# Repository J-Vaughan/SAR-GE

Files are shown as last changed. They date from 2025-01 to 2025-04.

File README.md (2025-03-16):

# SAR-GE

SAR-GE is a plan for a satellite using an SAR (Synthetic Aperture Radar) to
surveil Greenhouse Emissions over the entire domain of Canada. This project is
for Spacecraft Design I (AERO 3841) at Carleton University, and the defined
project variables are listed in the [Requirements](#Requirements) section.

> IMPORTANT: If you are currently taking AERO 3841, you are *not* permitted to
> use any part of this project to help you, for risk of academic misconduct.

This repository is meant to showcase my analysis and writing skills. ~~And, just
for fun, I'm going to try to do all of this with free, open-source software.~~
Why not use the tools given to me? I'll be using Ansys STK 12 and SolidWorks
2024.

## Mission Statement

From the project guidelines written by Professor T. Kaya, the main goal of this
mission is to monitor gas and oil pipelines from space. The payload is a SAR
consuming an average power of 350 W with a mass of 200 kg, housed in a
1 m by 0.5 m by 0.5 m (presumably) rectangular housing. The required resolution
is 5 m, and the ground swath width is 100 km. The coverage area per image is
100 x 100 km^2, and the whole country (Canada) needs to be imaged within
14 days. The master Earth station is the Gatineau Satellite Ground Station, with
Prince Albert station as a backup. The useful lifetime is 5 years, and the time
to deployment is 3 years.

# Requirements

The requirements listed in this section have been prescribed by the project
document.

## Communications
### Payload Data
- Required resolution of 5 m
- Area covered per image of 100 km x 100 km
- Ground swath width of 100 km
- Entire country must be imaged within 14 days

### Housekeeping Data
- The communications package must include the following data in addition to the
  payload data:
  | Data | Bits |
  | ---- | ---- |
  | Error Detection | 3 b per image size in bytes |
  | Latitude | 32 b per image |
  | Longitude | 32 b per image |
  | Altitude | 32 b per image |
  | Time | 64 b per image |
  | Synchronization | 24 b per image |
- Housekeeping data is sampled 100 times per minute with 16 bits
  per sample.

## Power
- Payload average power of 350 W.

## ADCS
- 1 degree accuracy for each of the three axes, and 0.1 degree accuracy for
  attitude determination.

## GNS
- Orbit should be maintained within 5 km of accuracy.

## Thermal
- Upper temperature limit of 50 degrees celsius, lower limit of -5 degrees, with
  a 5 degree margin on both values.
- Payload to be maintained at 20 degrees celsius with variation of less than
  1 degree on either side.

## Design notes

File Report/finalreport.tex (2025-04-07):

\documentclass[9pt]{article}
\usepackage[letterpaper, margin=2cm]{geometry}
\usepackage[utf8]{inputenc}
\usepackage[sfdefault]{inter}
\usepackage[T1]{fontenc}
\usepackage{amsmath}
\usepackage{graphicx, caption}
\usepackage{xcolor}
\usepackage{subcaption}
\usepackage{siunitx}
\usepackage{subfig}
\usepackage{booktabs}
\usepackage{tabularx}
\usepackage{multirow}
\usepackage{pdflscape}
\usepackage{mhchem}
\let\temp\rmdefault
\usepackage{fourier}
\let\rmdefault\temp

\usepackage[
  backend=biber,
  style=ieee
]{biblatex}
\addbibresource{spacecraft.bib}

% Title Page
\title{\Huge SARGE\\\Large Final Report}
\author{Jimmy Vaughan\\(101 156 687)}

\begin{document}
\begin{figure}[t]
  \centering
  
\end{figure}
\maketitle
\pagenumbering{gobble}
\clearpage
\tableofcontents
\clearpage
\pagenumbering{arabic}
\section{Introduction}
SARGE, \textbf{S}ynthetic~\textbf{A}perture~\textbf{R}adar:~\textbf{G}reenhouse~\textbf{E}missions, is a satellite platform designed to monitor for potential leaks of cross-Canada pipelines using synthetic aperture radar.
This report details a prelimnary design that should provide a solid starting point for further analysis and refinement.
Assumptions and estimations are necessary at this stage of development, and their presence is clearly noted in the following sections on analysis.

Preliminary design drawings are avaiable in the last appendix, Appendix~\ref{app:julia}.

\subsection{Primary Mission Objectives}
  The primary mission objective of SARGE is to monitor the entirety of Canada for the presence of greenhouse gasses that would indicate leaks in the transcontinental petrochemical pipelines.
  To this end, SARGE covers all of contiguous Canada, but does not directly cover the many islands in the far north of the territories.
  This should be acceptable, since there are no pipelines in those areas, and there is really only one pipeline above Hudson's Bay, ending just north of Mackenzie Bay, past Inuvik,~N.W.T.~\cite{pipelines}.
\subsection{Secondary Mission Objectives}
  Since SARGE covers the entirety of Canada (and Alaska, U.S.) any application of regular monitoring could be co-located on the satellite.
  Wildfire monitoring/detection, all industrial greenhouse gas emissions, and even meteorology.
  One of the only terrestrial applications SARGE is unsuited for is communications, as it is out of sight for about 2/3 of each day.

\section{Orbit Selection}
The assigned mission requirements state that this satellite is to image the entirety of Canada at least once every 14~days.
To satisfy this requirement, a geosynchronous orbit with a nonstandard high inclination (\ang{121}) was chosen.
The ground track of a conical SAR (shown in Figure~\ref{fig:groundtrack}) with a minimum elevation angle of \ang{75} covers the entirety of contiguous Canada.

\begin{figure}[hb]
  \centering
  \captionsetup{width=.75\linewidth,font={small},labelfont={bf}}
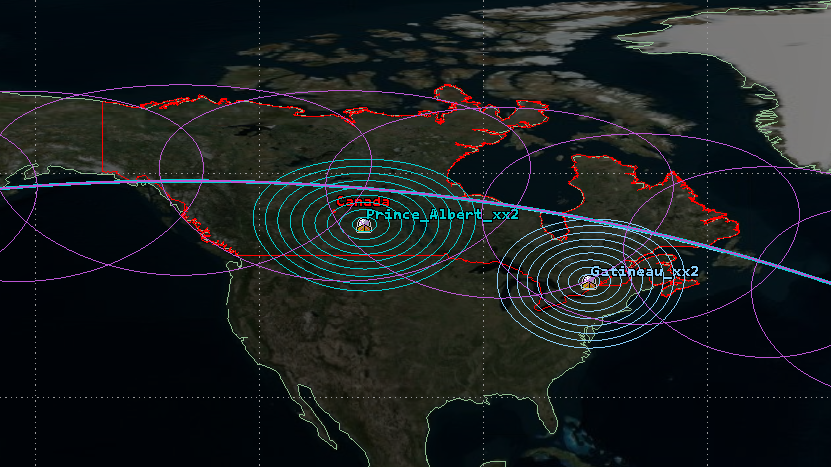
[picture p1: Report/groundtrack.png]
  
  \caption{Ground swath of SARGE over continental Canada. Ground stations are shown in teal and sky blue, and the majority of Canada is outlined in red ($A\approx\qty{8.342e6}{\square\kilo\metre}$). The magenta circles show the coverage of the SAR beam at some discrete points in time.}
  \label{fig:groundtrack}
\end{figure}

The orbital parameters are summarized in Table~\ref{tab:orbit}.
We can see that the chosen orbit is a circular retrograde orbit with a period of about one sidereal day.
This regularity allows the satellite to image, process, and transmit one~fourteenth of Canada each day, with a consistent and regular ground station access window.

\begin{table}[h]
  \centering
  \captionsetup{width=.75\linewidth,font={small},labelfont={bf}}
    \begin{tabular}{r S|r S}
      \toprule
      \multicolumn{4}{c}{Basic Orbital Parameters}\\
      \midrule
      Period $P$ & \qty{86170.5}{\second} & Arg. of Perigee $\omega$ & \ang{0} \\
      Eccentricity $\epsilon$ & \num{0.0} & LAN $\Omega$ & \ang{50} \\
      Inclinination $i$ & \ang{121} & True Anomaly $\nu$ & \ang{30} \\
      \midrule %\midrule
      \multicolumn{4}{c}{Derived Quantities}\\
      \midrule
      Orbit Radius $r$ & \qty{42166.26}{\kilo\metre} & Orbital Altitude $h$ & \qty{35788.12}{\kilo\metre} \\
      Velocity $v$ & \qty{3.074}{\kilo\metre\per\second} & Orbits per Day $n$ & \qty{1.002663}{\per\day} \\
      \bottomrule
    \end{tabular}
    \caption{Orbital parameters and convenient derived quantities.}
    \label{tab:orbit}
\end{table}

At high altitudes, like GEO, the gravitational forces of the Sun and the Moon become significant, but air drag is generally negligible~\cite[p. 81]{sse}.
As well, the high inclination of SARGE allows it to avoid most of the clutter in the GEO belt, since most of the objects are within <\ang{5} inclination~\cite[p. 140]{sme}.
Another advantage is the lack of an eclipse time in service (there may be a short eclipse during transit to orbit), as shown in Figure~\ref{fig:eclipse} in Section~\ref{sys:power}.
Stationkeeping requirements are also quite low, as explored in Appendix~\ref{app:stnkeep} and mentioned in Section~\ref{sys:prop}, since the oblateness of Earth is primarily a factor in lower inclination orbits.

\section{Spacecraft Bus}
\subsection{Mass and Power Budget}
According to David Everett of the NASA Goddard Space Flight Center, the first of the three steps of mass estimation is ``A rough order of magnitude based on payload mass''~\cite[p. 399]{sme}.
Given that sentiment, and approximate sizing of the power array (see Section~\ref{sys:power}), the initial mass estimate is based on data representative of mission type \textit{and} historical data given in Table~14-18, which can be found in Appendix~\ref{app:refs}, Figure~\ref{fig:1418}, and summarized in Table~\ref{tab:mass}, with comments noted in the third column.

\begin{table}[h]
  \centering
  \captionsetup{width=.75\linewidth,font={small},labelfont={bf}}
  %\begin{tabularx}{.8\linewidth}{l|r r X}
  \begin{tabular}{l|r r l}
    \toprule
    Subsystem & Mass\% & Mass & Comments \\
    \midrule
    Payload & \qty{32}{\percent} & \qty{200}{\kilo\gram} & Provided in requirements \\
    Structure \& Mechanisms & \qty{24}{\percent} & \qty{150}{\kilo\gram} & Taken from Table~14-18\\
    Thermal Control & \qty{6}{\percent} & \qty{36.}{\kilo\gram} & \qty{11}{\kilo\gram} taken from Power subsystem\\ 
    Power (incl. harness) & \qty{13}{\percent} & \qty{82}{\kilo\gram}&Less than usual since no eclipse\\
    TT\&C & \qty{4}{\percent} & \qty{25}{\kilo\gram}&Taken from Table~14-18\\
    Data Processing & \qty{3}{\percent} & \qty{19}{\kilo\gram}&''\\
    ADCS & \qty{8}{\percent} & \qty{50}{\kilo\gram}& \qty{13}{\kilo\gram} taken from Power\\
    Propulsion & \qty{7}{\percent} & \qty{44}{\kilo\gram}&Taken from Table~14-18\\
    Other & \qty{3}{\percent} & \qty{19}{\kilo\gram}&''\\
    \midrule 
    Total Dry Mass & \qty{100}{\percent} & \qty{625}{\kilo\gram} & \\
    Propellant & \qty{142}{\percent} & \qty{885}{\kilo\gram} & Double expected amount in Table~14-18\\
    Kick motor & \qty{12}{\percent} & \qty{75}{\kilo\gram} & Estimated mass of a jettisonable liquid motor\\
    \midrule 
    Wet Mass & & \qty{1585}{\kilo\gram} & \\
    \bottomrule
  \end{tabular}
  \caption{Preliminary mass budget estimation, based on provided payload mass and the listing for ``High Earth'' in the SME-SMAD~\cite{sme}.}
  \label{tab:mass}
\end{table}

The breakdown of the power subsystem is available in Table~\ref{tab:powerbreakdown} in Section~\ref{sys:power}.
Historical basis for the amount of propellant needed was insufficient for this particular satellite, primarily because of the steep inclination and the high-$\Delta V$ maneuvers required, detailed in Section~\ref{sys:prop}.
The total wet mass still comes in at far less than the SpaceX Falcon~9's maximum lift-off mass of \qty{5800}{\kilo\gram} (Table~\ref{tab:launchertrade}), so a shared launch is still feasible (especially given the compact nature of SARGE).

  Like the Mass Budget in Table~\ref{tab:mass}, the preliminary power budget below in Table~\ref{tab:power} is based on David~Everett's chapter of the SME-SMAD, Table~14-20 (Appendix~\ref{app:refs}, Figure~\ref{fig:1420}).
  This time, however, a modification to the suggested weights in Table~14-20 was made to accomodate the two one-axis solar array gimbals notes in Section~\ref{sec:configuration}. 
The payload power proportion was thus lessened by \qty{2}{\percent}, from \qty{35}{\percent} to \qty{33}{\percent} to give a corresponding power proportion of \qty{2}{\percent} to the Structures~\&~Mechanisms subsystem.
The solar array and battery sizing calculations are presented in Section~\ref{sys:power}.

\begin{table}[h]
  \centering
  \captionsetup{width=.75\linewidth,font={small},labelfont={bf}}
  \begin{tabular}{l|r r l}
    \toprule
    Subsystem & Power\% & Avg. Power & Comments \\
    \midrule
    Payload & \qty{33}{\percent} & \qty{350}{\watt} & Specified in requirements, mod. from Table~14-20 \\ 
    Structure \& Mechanisms & \qty{2}{\percent} & \qty{21}{\watt} & Mod. from Table~14-20 \\
    Thermal & \qty{14}{\percent} & \qty{148}{\watt} & Taken from Table~14-20 \\
    Power (incl. harness) & \qty{7}{\percent} & \qty{75}{\watt} & ''\\
    TT\&C & \qty{16}{\percent} & \qty{170}{\watt} & ''\\
    Data Processing & \qty{10}{\percent} & \qty{106}{\watt} &''\\
    ADCS & \qty{16}{\percent} & \qty{170}{\watt}&''\\
    Propulstion & \qty{2}{\percent} & \qty{21}{\watt} & ''\\
    \midrule
    Total & \qty{100}{\percent} & \qty{1061}{\watt} &\\
    \bottomrule
  \end{tabular}
  \caption{Preliminary power budget estimation, based on provided payload mass and the listing for ``High Earth'' in the SME-SMAD~\cite{sme}, modified to allow for powered mechanisms.}
  \label{tab:power}
\end{table}

\subsection{Configuration}\label{sec:configuration}
The configuration of SARGE is a nadir-pointing 3-axis stabilized solar-powered satellite.
The two solar arrays are gimbaled in one axis with a range of $\pm\ang{10}$ to account for the slight variation in the spacecraft's orientation with respect to the sun as it travels along its orbital path (this angle was found in Appendix~\ref{app:orbplanes}).
The size of the spacecraft can be estimated using the relations listed in Slideshow~3, Configuration, and shown in Table~\ref{tab:sizeest} below.

\begin{table}[h]
  \centering
  \captionsetup{width=.75\linewidth,font=small,labelfont=bf}
  \begin{tabular}{lll}
    \toprule
    Characteristic & Equation & Estimate \\
    \midrule
    Volume (\si{\meter\cubed}) & $V=0.01M$ & \qty{15.85}{\meter\cubed}\\
    Linear Dimension (\si{\meter}) & $L=0.25M^{1/3}$ & \qty{2.91}{\meter}\\
    Body Area (\si{\meter\squared}) & $A_b=V/L$ & \qty{5.44}{\meter\squared}\\
    Moment of Inertia (\si{\kilo\gram\meter\squared}) & $I=0.01M^{5/3}$ & \qty{2155}{\kilo\gram\meter\squared}\\
    \bottomrule
  \end{tabular}
  \caption{Estimate of spacecraft dimensions, where $M$ is spacecraft wet mass in \si{\kilo\gram}.}\label{tab:sizeest}
\end{table}

(Comment on the estimations). The mark is actually for assumptions for calculations? Idk, I modelled the satellite to fit the payload bruh.

An annotated isometric view of the preliminary design/layout is shown in Figure~\ref{fig:iso}.

\begin{figure}[h]
  \centering
  \captionsetup{width=.75\linewidth,font=small,labelfont=bf}
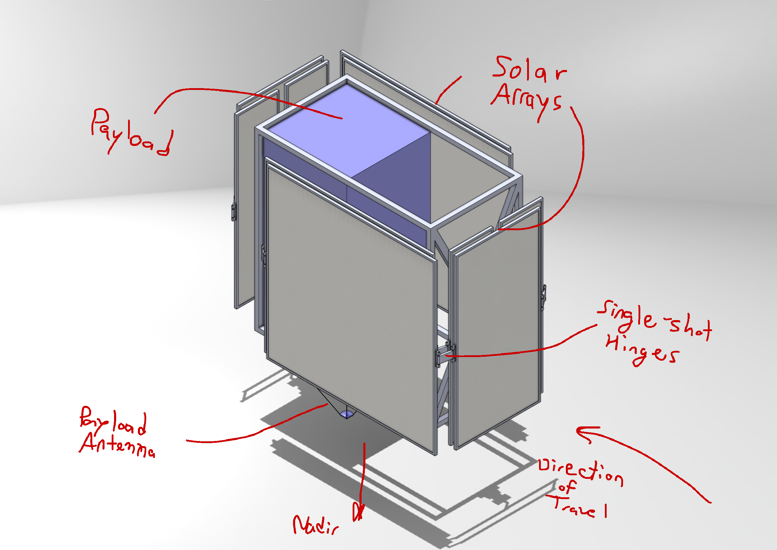
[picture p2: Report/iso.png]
  
  \caption{Isometric view of the satellite with annotation in red to aid understanding.}
  \label{fig:iso}
\end{figure}

As can hopefully be seen, the major components currently include 2 solar arrays, articulated only for launching, via single-shot hinges at each meeting point.
These arrays are gimbaled in one axis, shown in the front view, Figure~\ref{fig:front}.
The direction of travel is shown in Figure~\ref{fig:iso}, as well as the nadir pointing direction.

\begin{figure}[h]
  \centering
  \captionsetup{width=.75\linewidth,font=small,labelfont=bf}
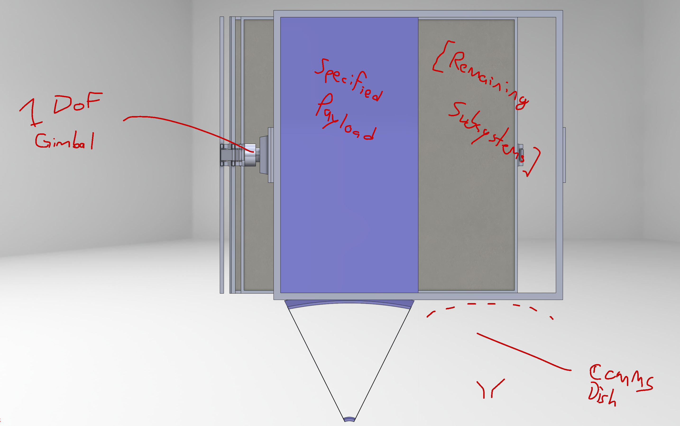
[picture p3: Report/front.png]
  
  \caption{Front view of SARGE with annotation in red. One of the solar panel arrays is hidden so as not to obstruct the interior of the frame.}
  \label{fig:front}
\end{figure}

Since the masses of the solar arrays are identical, and they are symmetric about the nadir axis, and since the mass proportion of the payload is only around \qty{32}{\percent} of the total dry mass, the remaining subsystems should make it so that the center of mass is not located within the payload container.
This means that an ADCS system with reaction wheels should be able to be located directly in line with all three axes relative to the center of inertia, so pointing should be easily controllable.
The remaining subsystems will all ideally fit in the remaining payload-sized area to the right of the payload in Figure~\ref{fig:front}.

More engineering drawings are available in Appendix~\ref{app:julia}.

Drawings (3.5)

Justification (2)

\subsection{Preliminary Design of Spacecraft Subsystems}
\subsubsection{Communications Subsystem}\label{sys:comms}
Based on both slide deck 6, ``TTC'', and select portions of the SME-SMAD, the uplink and downlink link budgets are summarized in Table~\ref{tab:link}.
As well, the downlink and uplink frequencies were chosen according to Professor~Jim~Wight's course handout for ELEC~4509.
It's noted in that handout that frequency ranges 7.25-7.30~GHz and 7.975-8.025~GHz are reserved for downlink and uplink satellite communications, respectively~\cite[II, p. 3]{commlinks}.
The downlink budget was conceived using the data rate/budget calculations in Appendix~\ref{app:linkbudget}.
As a quick summary, the amount of data transmitted per 14 days is about \qty{1}{\tera\byte}, with a daily access window of \qty{9.5}{\hour} and a downlink data rate during that window of about \qty{2.5}{\mega\byte\per\second}, for a (QPSK-encoded) bandwidth of about \qty{12}{\mega\hertz} on a \qty{7.275}{\giga\hertz} carrier.
\begin{table}[h]
  \centering
  \captionsetup{width=.75\linewidth,font=small,labelfont=bf}
  \begin{tabular}{c|rl|l}
    \toprule
    Uplink & Value & Unit & Comments \\
    \midrule
    $P_t$ & \num{23.01} & \si{\decibel\watt} & \qty{200}{\watt} ground transmitter assumed\\
    $G_t$ & \num{57.74} & \si{\decibel} & Eq.~\ref{eq:200}\\
    $L_\text{path}$ & \num{202.68} & \si{\decibel} & Eq.~\ref{eq:203}\\
    $L_\text{point}$ & \num{18.42} & \si{\decibel} & Eq.~\ref{eq:303}\\
    $L_\text{atmosphere}$ & \num{10.00} & \si{\decibel} & Assumed\\
    $k$ & \num{-228.60} & \si{\decibel\joule\per\kelvin} & \\
    $B$ & \num{37.00} & \si{\decibel\hertz} & Eq.~\ref{eq:201}\\
    $G_r$ & \num{6.49} & \si{\decibel} & Figure~\ref{fig:hfss}\\
    $T$ & \num{14.31} & \si{\decibel\kelvin} & Assumed\\
    \midrule
    ${C/N}_\text{achieved}$ & \num{33.42} & \si{\decibel} & Eq.~\ref{eq:uplinkachieved}\\
    ${C/N}_\text{required}$ & \num{8.16} & \si{\decibel} & Eq.~\ref{eq:202}\\
    \midrule
    Margin & \num{25.27} & \si{\decibel}& \\
    \bottomrule \toprule
    Downlink & Value & Unit & Comments\\
    \midrule
    $P_t$ & \num{20.00} & \si{\decibel\watt} & \qty{100}{\watt} of \qty{170}{\watt} estimated in power budget\\
    $G_t$ & \num{28.61} & \si{\decibel} & Eq.~\ref{eq:100}\\
    $L_\text{path}$ & \num{201.85} & \si{\decibel} & Eq.~\ref{eq:101}\\
    $L_\text{point}$ & \num{0.36} & \si{\decibel} & Eq.~\ref{eq:302}\\
    $L_\text{atmosphere}$ & \num{10.00} & \si{\decibel} & Assumed\\
    $k$ & \num{-228.60} & \si{\decibel\joule\per\kelvin} & \\
    $B$ & \num{70.77} & \si{\decibel\hertz} & Eq.~\ref{eq:downlinkbw}\\
    $G/T$ & \num{46.94} & \si{\decibel\per\kelvin} & Eq.~\ref{eq:minGT}\\
    \midrule
    ${C/N}_\text{achieved}$ & \num{41.17} & \si{\decibel} & Eq.~\ref{eq:downlinkachieved}\\
    ${C/N}_\text{required}$ & \num{11.52} & \si{\decibel} & Eq.~\ref{eq:102}\\
    \midrule
    Margin & \num{29.65} & \si{\decibel} & \\
    \bottomrule
  \end{tabular}
  \caption{Preliminary link budget, based on noted assumptions and analyses detailed in Appendix~\ref{app:linkbudget}.}
  \label{tab:link}
\end{table}

Unlike the preliminary design, for this design the uplink receiving antenna (i.e. the one on the spacecraft) is no longer the same as the parabolic downlink antenna.
The concern is that the parabolic antenna is too directional for the satellite to reliably establish telecommand communications while in transit to the desired orbit.
To mitigate this risk, several $4\lambda$ monopole antennas are now used to telecommand uplink.
While long monopole antennas are usually undesirable for ground communications (as they direct much of the signal vertically), they are a perfect application for satellite telecommand.
A length of $4\lambda$ was chosen based on the far-field radiation pattern shown in Figure~\ref{fig:radpat}.

\begin{figure}[h]
  \centering
  \captionsetup{width=.75\linewidth,font=small,labelfont=bf}
  \begin{subfigure}{.25\textwidth}
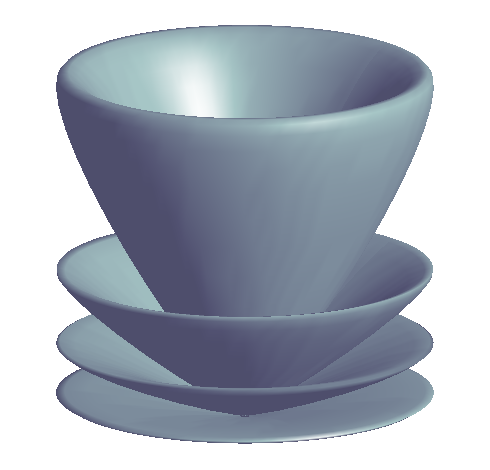
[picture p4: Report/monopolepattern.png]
    
    \caption{Far-field radiation pattern of $4\lambda$ monopole~[Chetvorno, \texttt{CC0}].}
    \label{fig:radpat}
  \end{subfigure}
  \hspace{4em}
  \begin{subfigure}{.35\textwidth}
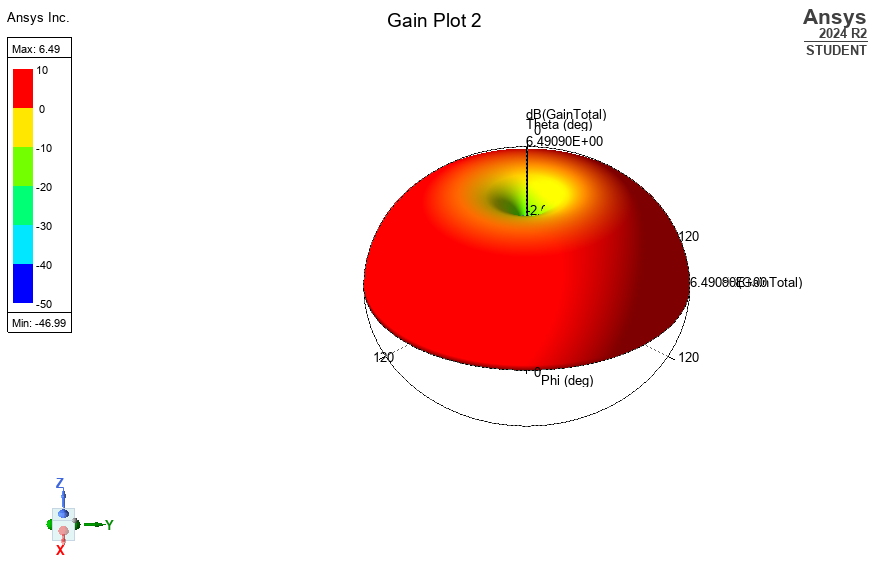
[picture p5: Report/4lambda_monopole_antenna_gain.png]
    
    \caption{HFSS simulation results for $4\lambda=\qty{15}{\milli\meter}$ monopole antenna at \qty{8}{\giga\hertz}. $G=\qty{6.49}{\decibel}$.}
    \label{fig:hfss}
  \end{subfigure}
  \caption{$4\lambda$ monopole antenna analysis.}
\end{figure}
 
To estimate the gain of a $4\lambda$ antenna for an \qty{8}{\giga\hertz} uplink, a model in Ansys HFSS was used, which resulted in the 3D gain plot in Figure~\ref{fig:hfss}, for a maximum gain of \qty{6.49}{\decibel}.
Why it doesn't match Figure~\ref{fig:radpat}, I'm not sure, but it should still serve well as the telecommand antenna(s), since the margin is still quite high.

The uplink ${C/N}_\text{achieved}$ was calculated using the following expression, where square brackets indicate logarithmic quantities:
\begin{equation}\label{eq:uplinkachieved}
  [C/N]_\text{achieved}=[P_t] + [G_t] + [G_r] - [L_\text{path}] - [L_\text{point}] - [L_\text{atmosphere}] - [k] -[T]-[B]
\end{equation}
Whereas the downlink ${C/N}_\text{achieved}$ was calculated using a slightly different methodology, where the minimum certifiable $G/T$ figure is found by~\cite[I, p. 40]{commlinks}:
\begin{equation}\label{eq:minGT}
  \frac GT\ge \qty{40.7}{\decibel}+20\log{\frac f4}
\end{equation}
where $G/T$ is in \si{\decibel\per\kelvin}, and $f$ is in \si{\giga\hertz}.
Since that's the minimum figure of merit to be certified for a ground station, I took that as the figure of merit for Gatineau.
Then,
\begin{equation}\label{eq:downlinkachieved}
  [{C/N}]_\text{achieved}=[P_t]+[G_t]+\left[\frac GT\right]-[L_\text{path}]-[L_\text{point}]-[L_\text{atmosphere}]-[k]-[B]
\end{equation}
The ground station transmit power and the satellite noise temperature were both assumed based on representative data in the SME-SMAD.
The $G/T$ figure in equation~\ref{eq:minGT} is specifically for Telesat certification, but that should be applicable given the age of the Gatineau station and Telesat's presence in the area.
The \qty{10}{\decibel} atmosphere loss is mostly an expression of an allowable margin for atmospheric losses.
Further analysis would be required to get an accurate estimate of expected atmospheric losses.
Typically, they should be pretty low, since the signal really doesn't spend much time passing through the atmosphere at all.

\subsubsection{Power Subsystem}\label{sys:power}

Given SARGE's highly inclined orbit, there is in fact no eclipse time at all since the orbital plane is at about a right angle to the ecliptic plane.
The solar panels were sized according to Table~21-12 in the SME-SMAD for preliminary solar array sizing (Appendix~\ref{app:refs}, Figure~\ref{fig:2112}).
The process is laid out in Table~\ref{tab:powersub}.

\begin{table}
  \centering
  %
  \begin{tabular}{c|ll|rl|l}
    \toprule
    Step & Description & & Value & Unit & Notes\\
    \midrule
    \multirow{3}{7em}{Requirements and Constraints} & Power required & $P_\text{req}$ & 1061 &\si{\watt} & \\
    & Eclipse duration & $T_e$ & 0 & \si{\second} & \\
    & Design lifetime & $L$ & 5 & \si{yr} & \\
    \midrule
    \multirow{4}{7em}{Power to be produced} & Light duration & $T_d$ & 86170.5 & \si{\second} & $=P-T_e$\\
    & Path efficiency, eclipse & $X_e$ & 0.65 & & Unused\\
    & Path efficiency, day & $X_d$ & 0.85 & & Direct energy transfer\\
    & Required array power & $P_\text{sa}$ & 1,248 & \si{\watt} & $=P_\text{req}/X_d$\\
    \midrule
    \multirow{2}{7em}{Type of solar panel} & GaAs efficiency & $\eta$ & 18.5 & \si{\percent} & \\
    & Worst case power per cell & $P_0$ & 244.4 & \si{\watt\per\meter\squared} & $=\eta\cdot 1321$ SS\\
    \midrule
    \multirow{3}{7em}{BOL areal capacity} & Inherent degredation & $I_d$ & 0.72 & & Nominal\\
    & Worst case incident angle & $\theta$ & 10 & \si{\degree} & Appendix~\ref{app:orbplanes}\\
    & BOL performance & $P_\text{BOL}$ & 173.3 & \si{\watt\per\meter\squared} & $=P_0I_d\cos\theta$\\
    \midrule
    \multirow{3}{7em}{EOL production} & Degradation per year & $D$ & 2.75 & \si{\percent} & GaAs\\
    & Life degradation & $L_d$ & 0.87 & & $=(1-D)^L$\\
    & EOL performance & $P_\text{EOL}$ & 150.7 & \si{\watt\per\meter\squared} & $=L_dP_\text{BOL}$\\
    \midrule
    & Area needed & $A_\text{sa}$ & 8.28 & \si{\meter\squared} & $=P_\text{req}/P_\text{EOL}$\\
    & Mass & $M_\text{sa}$ & 22.36 & \si{\kilo\gram} & GaAs SJ, \qty{2.7}{\kilo\gram\per\meter\squared}\\
    & Price & & 1.063 & MM\$US & GaAs SJ, \qty{852}{\$\per\watt BOL}\\
    \bottomrule
  \end{tabular}
  \caption{Power subsystem solar array sizing.}
  \label{tab:powersub}
\end{table}

The only time a battery may be needed is during the ecliptic transfer orbit from launch to GEO.
The period $T$ of that orbit ($a=\qty{24364}{\kilo\meter}$, $T=2\pi\sqrt{a^3/\mu}$) is about \qty{10.5}{\hour}.
Being generous, we'll allow for 1.5 orbits (\qty{17.3}{\hour}) of primary battery power (i.e. one ``go-around'').
For this, we'll choose a \ce{LiSO2} battery system (chosen for the ``day-scale'' energy storage performance) with a specific energy density of \qty{350}{\watt\hour\per\kilo\gram}.
Assuming the payload is off during this transfer orbit, the power needed is \qty{711}{\watt}, and thus we need to store \qty{12.3}{\kilo\watt\hour} of energy, giving a battery mass of \qty{35}{\kilo\gram} (\qty{43}{\percent} of power subsystem mass).
The solar array takes up \qty{30}{\percent} of the power subsystem mass (with \qty{10}{\percent} margin), and the remaining \qty{22}{\kilo\gram} (\qty{27}{\percent}) is left for the harness with \qty{10}{\percent} margin.
Ideally, the spent primary battery would be ejected along with the kick motor to ease the fuel requirements for stationkeeping, but not for this current analysis.
The bus will be \qty{28}{\volt} to minimize current drawn and resistive losses, and since there's no eclipse, the bus will operate on direct energy transfer, without regulation.

\subsubsection{Thermal Control Subsystem}\label{sys:thermal}
To analyze the thermal situation of SARGE, the entire spacecraft body was assumed to be diffuse, gray, and isothermal.
Each principal axis was analyzed individually, for a total of 6 regions covering (1) the sides of sarge (along direction of travel); (2) the frontal (sun-facing) area of the solar panels only; (3) the frontal area of the spacecraft body only; (4) the bottom of the spacecraft (nadir pointing); (5) the entire back area of the solar panels and body; and (6) the top surface of the spacecraft.
The thickness of the solar panels was considered negligible.

The worst-case hot and cold calculations are shown in Table~\ref{tab:thermal}.

\begin{landscape}
  \begin{table}[h]
    \centering
    %\captionsetup
    \begin{tabularx}{1.00\linewidth}{ll|r|rrrrrr|l|X}
      \toprule
      WCH & & Total & Sides & F. Solar & F. Body & Bottom & Back & Top & Unit & Notes\\
      \midrule
      Material & & & 5ST & GaAs & 5ST & Z93 & Z93 & 2ST & & Material key follows table\\
      \midrule
      Solar Irradiance & $G_s$ & & 49.59 & 1421 & 1421 & 2.48 & 0 & 2.48 & \si{\watt\per\meter\squared} & WS, \ang{2} nadir error, \ang{0.1} rest error\\
      Solar absorption & $\alpha_s$ & & .07875 & .85575 & .07875 & .18375 & .18375 & .07875 & & \qty{5}{\percent} degradation EOL values\\
      IR emissivity & $\varepsilon_\text{IR}$ & & .741 & .57 & .741 & .874 & .874 & .627 & & GaAs ass. .6, and \qty{5}{\percent} EOL deg.\\
      Earth albedo & $\mathrm{a}$ & & & & & 35 &  & & \si{\percent} & +5\% albedo\\
      Earth IR flux & $\dot q_E$ & & 9 & 9 & 9 & 258 & 9 & 0 & \si{\watt\per\meter\squared} & High\\
      Generated power & $\dot Q_w$ & 844.33 & & & & & & & \si{\watt} & Justification following\\
      Area & $A_\text{sc}$ & 20.5 & 0.5 & 8.5 & 1 & 0.5 & 9.5 & 0.5 & \si{\meter\squared} & \\
      Earth ang. radius & $\rho$ & .15184 & & & & & & & \si{rad} & $=\sin^{-1}(R_E/r)$\\
      \midrule
      Sun IN & & 10,450 & 2 & 10,336 & 112 & 0 & 0 & 0 & \si{\watt} & $=G_s\alpha_s A_\text{sc}$\\
      Earth IR IN & & 0 & 0 & 0 & 0 & 0 & 0 & 0 & \si{\watt} & $=(\dot q_E\sin^2\rho)(1-\cos\rho)\varepsilon_\text{IR}/2$\\
      Albedo IN & & 0 & 0 & 0 & 0 & 0 & 0 & 0 & \si{\watt} & $=G_sA_\text{sc}\mathrm{a}\alpha_s(1-\cos\rho)\sin^2\rho/2$\\
      Total heat & $\dot Q_\text{out}$ & 11,295 & & & & & & & \si{\watt} & Including SC power gen\\
      \midrule
      Eff. emissive area & $\varepsilon_\text{IR}\cdot A_\text{sc}$ & 15.01 & 0.3705 & 4.845 & 0.741 & 0.437 & 8.303 & 0.3135 & \si{\meter\squared} & \\
      WCH Temperature & $T$  & 339.4 & & & & & & & \si{\kelvin} & $=\sqrt[4]{\dot{Q}_\text{out}/\sum{\varepsilon_\text{IR}A_\text{sc}}}=\qty{66.26}{\celsius}$\\
      \bottomrule\toprule
      WCC & & Total & Sides & F. Solar & F. Body & Bottom & Back & Top & Unit & Notes \\
      \midrule
      Solar Irradiance & $G_s$ & & 46.10 & 1321 & 1321 & 2.31 & 0 & 2.31 & \si{\watt\per\meter\squared} & SS, same errors\\
      Solar absorption & $\alpha_s$ & & .075 & .815 & .075 & .175 & .175 & .075 & & BOL\\
      IR emissivity & $\varepsilon_\text{IR}$ & & .78 & .65 & .78 & .92 & .92 & .66 & & BOL\\
      Earth albedo & $\mathrm{a}$ & & & &  & 25 & & & \si{\percent} & -5\% albedo\\
      Earth IR flux & $\dot q_E$ & & 7.54 & 7.54 & 7.54 & 216 & 7.54 & 0 & \si{\watt\per\meter\squared} & Low\\
      \midrule
      Sun IN & & 9,252 & 2 & 9,151 & 99 & 0 & 0 & 0 &\si{\watt} & Same calculations as WCH\\
      Total heat & $\dot Q_\text{out}$ & 10,097 & & & &  & & & \si{\watt} & Including SC power gen\\
      \midrule
      Eff. emissive area & $\varepsilon_\text{IR}\cdot A_\text{sc}$&16.23 & 0.39 & 5.525 & 0.78 & 0.46 & 8.74 & 0.33 & \si{\meter\squared}&\\
      WCC Temperature & $T$ & 323.7 & & & & & & & \si{\kelvin} & $=\qty{50.51}{\celsius}$\\
      \bottomrule
    \end{tabularx}
    \caption{Worst-case thermal calculations.}
    \label{tab:thermal}
  \end{table}
\end{landscape}
5ST and 2ST are 5~mil Silver-coated Teflon and 2~mil Silver-coated Teflon, respectively, and Z93 is the Z93~white paint.
Values for these materials were taken from Table~22-14 in SME-SMAD (Appendix~\ref{app:refs}, Figure~\ref{fig:2214}).
The first configuration for SARGE had the back surfaces covered in 2~mil Silver-coated Teflon, which resulted in a WCH temperature of \qty{81}{\celsius} and a WCC of \qty{64}{\celsius}.
Given the typical operating temperature ranges in Slideshow~10, Thermal, this range seemed high.
Changing the back surfaces to Z93~white paint resulted in a much milder steady-state situation.

The generated power of the spacecraft is lower than the total power in the power budget as I assumed that the \qty{100}{\watt} downlink transmitter power is emitted as signal (RF-waves) and that a third of the payload power (\qty{117}{\watt}) is similarly emitted as radar waves.
Since SARGE is quite far from the Earth, it makes sense that the reflected sunlight and Earth IR emissions are very low, essentially rounding errors. Their contributions are still included in the totals, but it is essentially negligible.

Galium Arsenside panels were assumed to be approximately \qty{100}{\percent} absorptive of solar energy~\cite{gaas}, with the \qty{18.5}{\percent} efficiency of electrical conversion taken into account.
The IR emissivity was estimated to be around 0.6, the lower end of Silicon cells.

\subsubsection{Guidance and Navigation Subsystem}\label{sys:nav}
Relevant perturbations and explanation (1)

orbit control strategy (maintenance, actuators/sensors) (2)

choice of autonomous or groun control with explanation/justification (2)

de-orbiting strategy and explanation (1)

\subsubsection{Propulsion Subsystem}\label{sys:prop}
Orbital transfer from injected orbit (calculations and justification for maneuver choice) (3)

Propellant mass calculations for maintenance and deo-orbiting (3) take from appendix and put here

Given the GTO... stationkeeping... disposal...

Can't use ion engine because of power requirements...\cite{next}

yeah
\subsubsection{Attitude Determination and Control Subsystem}\label{sys:adcs}
attitude control strategy and explanation/justification (2)

actuator selection and explanation/justification (1)

sensor selection and justification/explanation (2)

pointing requirements, maneuvers needed and explanation/justification (1)

\subsubsection{Structures}\label{sys:struct}
material selections and explanation/justification (2.5)

mechanism selection and explanation/justification (2.5)

\section{Launcher Selection Trade Study}\label{sec:launcher}
A selection of launch platforms still in use as of 2025 were considered, with the key parameters summarized in Table~\ref{tab:launchertrade}.
All launchers deliver their payload to GTO, with fairly minor differences in delivered transfer orbit, with the exception of the Ariane~62.

\begin{table}[h]
  \centering
  \captionsetup{width=.75\linewidth,font=small,labelfont=bf}
  \begin{tabular}{lc|cccc|ccr}
    \toprule
    Platform & Country & $i$ (\si{\degree}) & $h_p$ (\si{\kilo\meter}) & $h_a$ (\si{\kilo\meter}) & $\omega_p$ (\si{\degree}) & $M$ (\si{\kilo\gram}) & $D$ (\si{\meter}) & Cost \\
    \midrule
    SpaceX Falcon 9~\cite{spacex} & USA & \num{28.5} & \num{185} & \num{35788} & \num{0} & \num{5800}\textdagger & \num{3.7} & \num{69.75}~\cite{spacexprice} \\
    Ariane~62~\cite{ariane} & France & \num{6} & \num{250} & \num{35786} & \num{178} & \num{4500} & \num{5.4} & \num{88}\hspace{1.55em}\cite{arianeprice}\\
    Atlas V 401~\cite{atlasv} & USA & \num{27} & \num{185} & \num{35786} & \num{180} & \num{4750} & \num{4.0} & \num{109}\hspace{.6em} \cite{atlasvprice}\\
    Long March 3B~\cite{longmarch} & China & \num{28.5} & \num{200} & \num{35786} & \num{178} & \num{5100} & \num{4.0} & \num{70}\hspace{.9em}\cite{longmarchprice}\\
    \bottomrule
  \end{tabular}
  \caption{Selected launch platform comparison. \textdagger: includes payload adapter. Prices in millions USD, not adjusted for inflation.}
  \label{tab:launchertrade}
\end{table}

explain shared launch reasoning, or actually evaluate if shared launch is even possible given the huge propulsion requirements

\section{Schedule}
worth 2 marks :/

order of various design stages, can include chart (2)

\section{Cost}
worth 2 marks :/

major cost elements (launcher, payload, testing, insurance) (1)

reliable sources references (textbook, other missions, etc) (1)

\section{Conclusions}
summarize major values/parameters (3)

discuss future work (2)

Although further analysis is required to ensure that the current configuration can reject/retain enough heat, and the delta V budget is yet to be done, the current iteration of SARGE looks to be reasonable.
The mass distribution and total mass falls within the ranges typical of a GEO mission.
The total estimated power draw is somewhat lower than what is mentioned in the course slides.
The link budget has good margins, even after adding an assumed atmospheric loss.

\clearpage
\appendix

\printbibliography
\clearpage
\section{Orbital Perturbations and $\Delta V$}\label{app:orbpert}

SME-SMAD equations (9-46) and (9-47) on pg.~219 give approximate worse case $\Delta V$ relations per year~\cite{sme}:
\begin{align}
  {\Delta V}_\text{Moon} &= 102.67\cos\alpha\sin\alpha\hspace{2em}\text{(m/s per year)}\\
  {\Delta V}_\text{Sun} &= 40.17\cos\gamma\sin\gamma\hspace{2.7em}\text{(m/s per year)}
\end{align}
where $\alpha$ is the angle between the orbit plane and the Moon's orbit, and $\gamma$ is the angle between the orbit plane and the ecliptic.

\subsection{Stationkeeping}\label{app:stnkeep}
The angles estimated in Appendix~\ref{app:orbplanes} and illustrated in Figure~\ref{fig:moonorbit}, substituted into the preceding expressions, yield:
\begin{equation}
  {\Delta V}_\text{Moon} = 102.67\cos{\ang{92.42}}\sin{\ang{92.42}} = \qty{4.331}{\meter\per\second\per yr}
\end{equation}
\begin{equation}
  {\Delta V}_\text{Sun} = 40.17\cos{\ang{97.56}}\sin{\ang{92.42}} = \qty{5.239}{\meter\per\second\per yr}  
\end{equation}
And then, for the design lifetime of 5 years, the total $\Delta V$ for North-South stationkeeping is the product of the sum of the above:
\begin{equation}
  {\Delta V}_{NS} = ({\Delta V}_\text{Moon} + {\Delta V}_\text{Sun}) \times \qty{5}{yr} = \qty{47.85}{\meter\per\second}
\end{equation}
This is significantly less than the example value of about \qty{51.48}{\meter\per\second\per yr} given in the SME-SMAD for a GEO orbit with an inclination $i$ of \ang{0}~\cite{sme}.
This makes sense, since for a equatorial GEO orbit the Ecliptic and Lunar planes would be between \ang{23.44} and \ang{28.68}, whereas SARGE's highly inclined orbital plane is at nearly right angles to the Ecliptic and Lunar planes, somewhat balancing the perturbing forces of both.

The transverse (East-West) stationkeeping requirement is mentioned as about \qty{10}{\percent} of the North-South stationkeeping requirements~\cite{sme}, however I believe that the high inclination of SARGE will work against us in this scenario, as the oblateness of Earth around the equator will have a more pronounced effect for orbits that do not closely follow the equator.
As well, this oblateness likely has an effect on the North-South stationkeeping, since we're dealing with neither a polar nor equatorial orbit.
For this reason, I'm going to estimate the East-West stationkeeping to be equal to the North-South:
\begin{equation}
  {\Delta V}_{EW} = {\Delta V}_{NS} = \qty{47.85}{\meter\per\second}%pg 219
\end{equation}
This ought to roughly account for the stationkeeping requirements of the spacecraft at this stage of design. 

\subsection{Decommissioning}

The SME-SMAD recommends handling the special scarcity and properties of the GEO orbit (specifically its vulnerability to debris and junk) by raising spacecraft \qty{500}{\kilo\metre} above GEO at the end of their life.
The $\Delta V$ required for that is
\begin{equation}
  {\Delta V}_\text{disposal} = \qty{18}{\metre\per\second}
\end{equation}
from SME-SMAD page 233 for decommissioning a GEO satellite~\cite{sme}, and the propellant mass will be found at a later date after an in-depth $\Delta V$ analysis.

\subsection{Orbital Transfer}
The transfer from the SpaceX GTO orbit in Table~\ref{tab:launchertrade} will be a combined plane-change and elliptical-to-circular maneuver.
The $\Delta V$ required for such a change is~\cite{aero3240}:
\begin{equation}
  \Delta V=\sqrt{v_1^2+v_2^2-2v_1v_2\cos{\Delta i}}
\end{equation}
where $\Delta i=\ang{121}-\ang{28.5}=\ang{92.5}$, and $v_1,\,v_2$ are the orbital velocities of the transfer orbit and final orbit respectively.
The full calculation is scanned and attached in Appendix~\ref{app:orbcalcs}.
Hand calculations were chosen as a change of pace.
The final result is a $\Delta V$ of \qty{3.5253}{\kilo\meter\per\second}.

\section{Power and Configuration Implications}\label{app:powerandconf}
\subsection{Power Collection and Storage}\label{app:powercollection}
Given the estimated total average power presented in Table~\ref{tab:power}, \qty{1061}{\watt}, the required solar panel coverage can be estimated following the example in slide deck 7, ``Power'', where the following expression is provided on slide~17:
\begin{equation}
  {PD}_\text{out}={PD}_\text{in}\eta\cos\theta
\end{equation}
where ${PD}_\text{out/in}$ is the power density of out of and into the solar array in \si{\watt\per\meter\squared}, $\eta$ is the power conversion efficiency of the cells, and $\theta$ is the solar incident angle.
Taking the incident solar power as \qty{1366}{\watt\per\meter\squared}, and the achieved efficiency of GaAs cells provided in slide~18 of \qty{18.5}{\percent}, with a worst-case incident angle of about \ang{10} (since the angle of the orbital plane to the ecliptic is \ang{97.56}, found in Appendix~\ref{app:orbplanes}), then
\begin{equation}
  {PD}_\text{out}=\qty{1366}{\watt\per\meter\squared}\cdot\qty{18.5}{\percent}\cdot\cos(\ang{10})= \qty{248.87}{\watt\per\meter\squared}
\end{equation}
Then, dividing the total average power required by the spacecraft (and noting that the spacecraft spends no time in eclipse), the minimum required illuminated area of the solar array is
\begin{equation}
  A_\text{solar,min} = \frac{P_\text{total}}{PD_\text{out}} = \qty{4.26}{\square\meter}
\end{equation}
Since the spacecraft is orbiting in a plane nearly perpendicular to the ecliptic plane, a 1~DoF mechanism for the pointing of the solar array with an angular envelope of $\pm\ang{10}$ should be sufficient to ensure optimal solar collection.
This fact and the lack of eclipse time is well conveyed by Figure~\ref{fig:eclipse} below, showing no part of the orbital track lying in eclipse.

\begin{figure}[h]
  \centering
  \captionsetup{width=.75\linewidth,font=small,labelfont=bf}
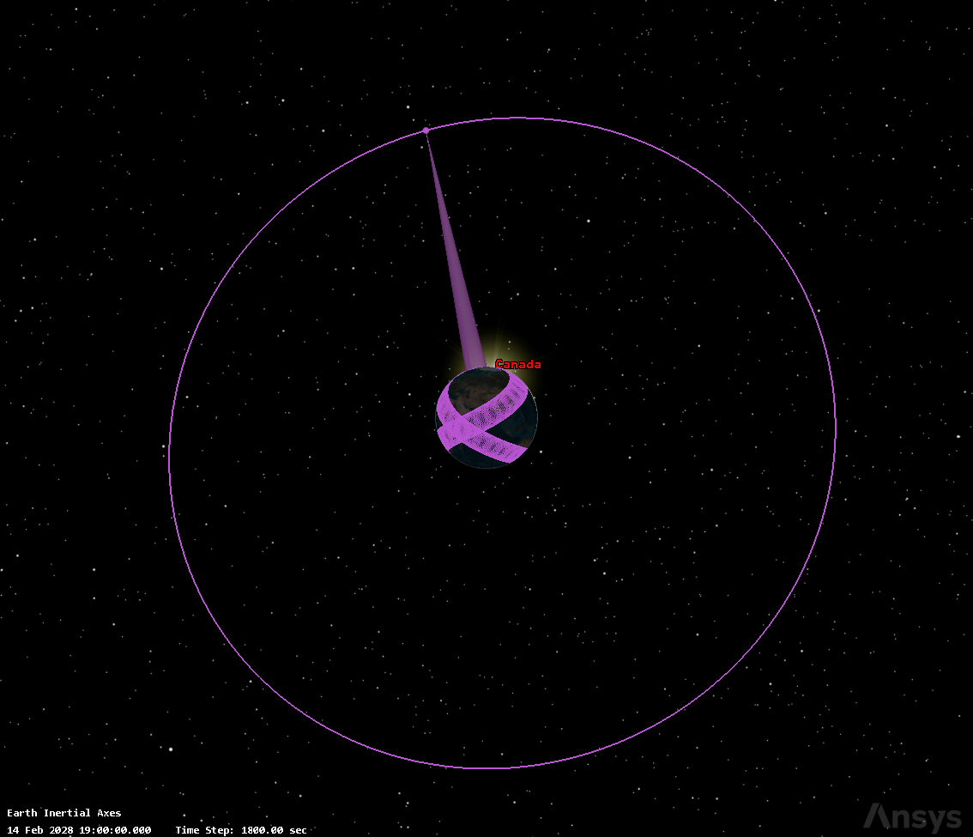
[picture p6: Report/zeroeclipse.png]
  
  \caption{Demonstration of zero eclipse time via STK 3D view. The sun is visible just over the horizon.}
  \label{fig:eclipse}
\end{figure}

\subsection{Configuration Choices}
In order to accomodate the necessary surface area of the solar panels in a compact way with margins to account for structural frames that would block cells of the solar array, and to pre-emptively take into account the packing of the spacecraft into a launch platform, a quick sketch (Figure~\ref{fig:solarsketch}) showed that the structure should follow roughly a form factor of $\SI{1}{\meter}\times\SI{1}{\meter}\times\SI{0.5}{\meter}$.
This allows the compact packing of nominally \SI{6}{\square\meter} of solar panels, which well exceeds the required \SI{4.26}{\square\meter}.
In later analysis, it will be shown how much of a margin we have to block that area with support structures when EOL conditions and degradation is taken into account.

Table~21-5 in the SME-SMAD notes that travelling wave tube amplifiers (TWTA)s are about 50-60\% efficient for X-band and weigh about \qty{2.5}{\kilo\gram} including power converter~\cite[p. 637]{sme}.
Table~16-16 in the SME-SMAD notes that parabolic reflectors weigh between 10-30~kg~\cite[p. 484]{sme}.

\clearpage
\section{Fun!}
This section is named ``Fun!'' unironically -- these were fun.

\subsection{Fun Annulus Geometry}\label{app:annulus}
To approximate the arc angle subtended by the \ang{10} elevation $\delta$ access requirement, I created a quick sketch shown in Figure~\ref{fig:annulus} to wrap my head around the geometry.
I then used the formula for worst-case distance $d$ from slide deck 6 to find the corresponding half angle $\gamma$:
\begin{equation}
  d=R_\text{Earth}\left(
    \sqrt{\left(\frac{r}{R_\text{Earth}}\right)^2-\cos^2\delta}
    -\sin\delta
  \right)
\end{equation}
From my sketch,
\begin{equation}
  \gamma = \sin^{-1}\left(\frac{d\sin(\ang{90}+\delta)}{r}\right)
\end{equation}
And thus the access ratio is the ratio between the access arc and the total arc (circumference):
\begin{equation}
  \text{Access Ratio} = \frac{2\gamma r}{2\pi r} = \qty{39.69}{\percent}
\end{equation}

\begin{figure}[h]
  \centering
  \captionsetup{width=.75\linewidth,font=small,labelfont=bf}
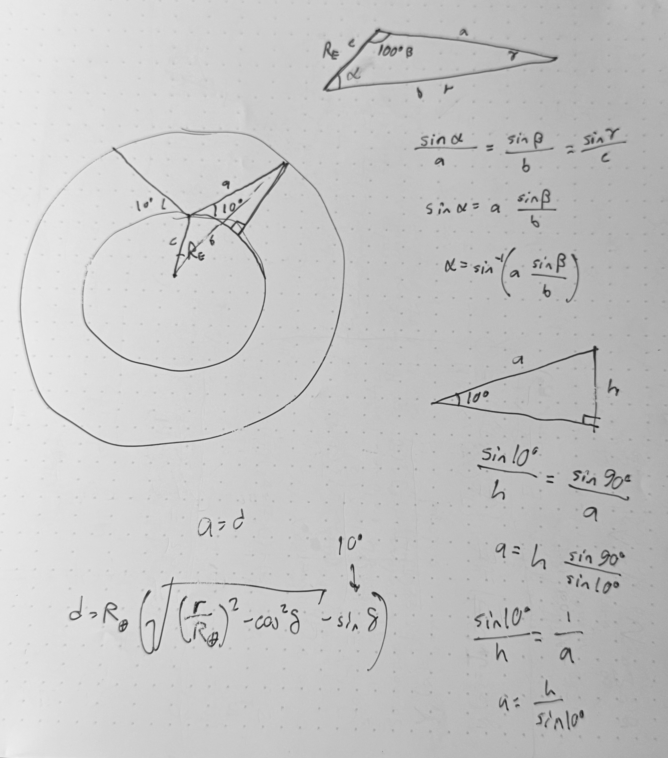
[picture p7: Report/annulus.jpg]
  
  \caption{Figuring out the geometry to find the half-angle from the center of the Earth given the radius and elevation [Own work].}
  \label{fig:annulus}
\end{figure}

This makes a lot of sense -- SARGE is far away, the elevation angle of \ang{10} is pretty generous, and the groundtrack passes fairly close to Gatineau station (on a global scale, at least).

\subsection{Fun Orbital Plane Geometry}\label{app:orbplanes}

To find $\alpha$ and $\gamma$ for the orbital perturbation estimations in Appendix~\ref{app:orbpert}, I estimated the angles between SARGE's orbital plane and the Sun and the Moon using the Ecliptic plane and Lunar orbit inclination values found in a figure (with no listed author) from Wikipedia.

\begin{figure}[hb]
  \centering
  \captionsetup{width=.75\linewidth,font={small},labelfont={bf}}
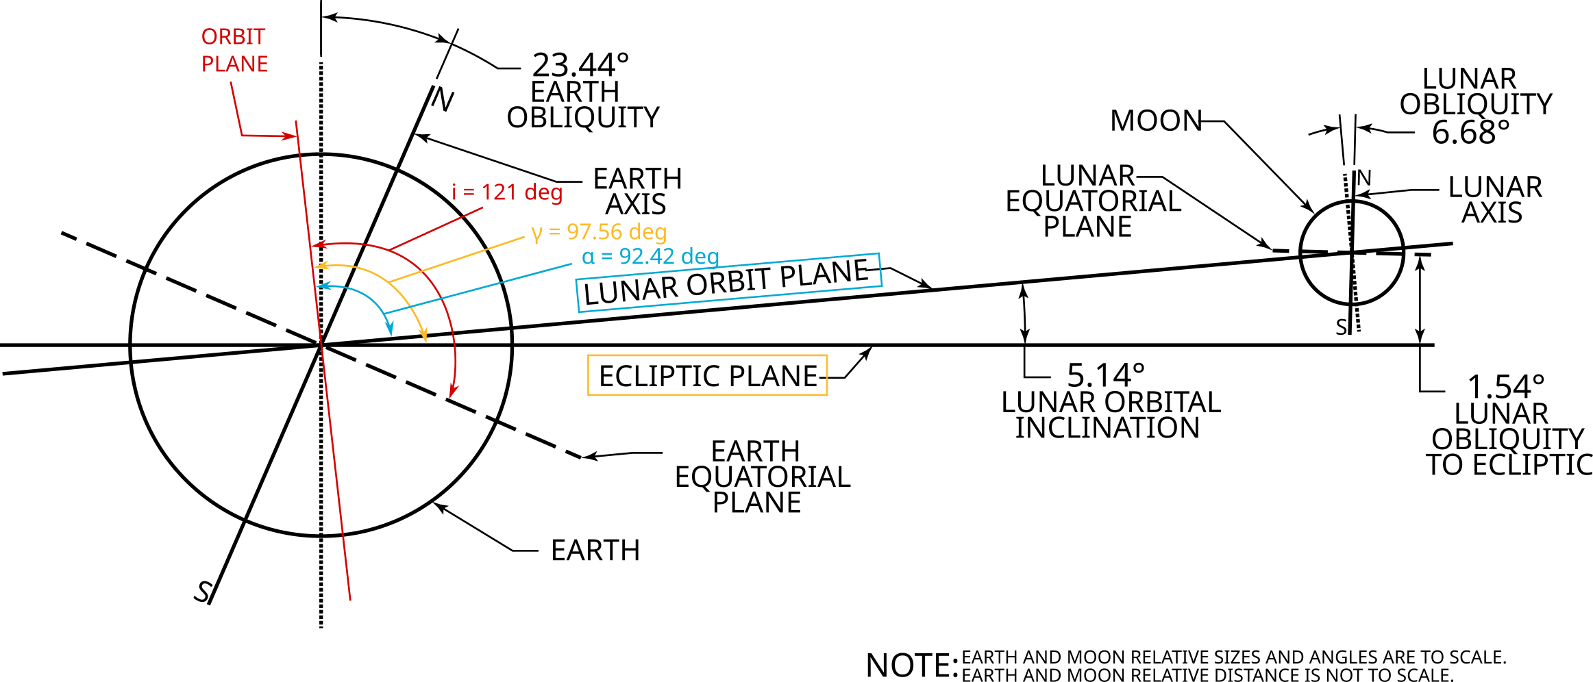
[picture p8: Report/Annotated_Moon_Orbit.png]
  
  \caption{Angles between the orbit plane of SARGE and the Lunar orbit plane ($\alpha$) and the Ecliptic plane ($\gamma$). [Author unknown, \texttt{CC0}, annotations (in colour) added]}
  \label{fig:moonorbit}
\end{figure}

From Figure~\ref{fig:moonorbit}, we can estimate that the angle between SARGE's orbit plane and the Ecliptic plane ($\gamma$) to be \ang{97.56}, and between SARGE's orbit plane and the Lunar orbit plane ($\alpha$) as \ang{92.42}.

\section{Link Budget}\label{app:linkbudget}
\subsection{Down}
The initial step of developing the link budget is to determine how much payload data we need to download.
The area of Canada proper, shown in red in Figure~\ref{fig:groundtrack}, is about \qty{8.342e6}{\kilo\meter\squared}.
From the mission requirements, we need to image that entire area (at least) once every \qty{14}{\day}.
Assuming that the payload is capable of steering its beam in order to cover swaths of \qty{100}{\kilo\meter} width, and considering an image to be $\qty{100}{\kilo\meter}\times\qty{100}{\kilo\meter}$, with a linear resolution of \qty{5}{\meter} such that each pixel is $\qty{25}{\meter\squared}$ and contains \qty{16}{\bit} of data, we estimate the amount of data required to image all of Canada using the following:
\begin{equation}
  \text{Image Pixels} = \frac{\text{Image Area}}{(\text{Linear Resolution})^2}=\qty{4.0e8}{pixels}
\end{equation}
Then, the size of each image:
\begin{equation}
  \text{Image Size} = \text{Pixel Size}\times\text{Image Pixels} = \qty{800}{\mega\byte}
\end{equation}
Then, the images required to cover Canada, with a 4\% swath overlap accomodation:
\begin{equation}
  \text{Images per Canada} = \frac{A_\text{Canada}}{\text{Image Area}}\times 1.04 \approx \qty{868}{images}
\end{equation}
And thus, the amount of data required to image Canada once:
\begin{equation}
  \text{Canada Size} = \text{Images per Canada} \times \text{Image Size} = \qty{694.05}{\giga\byte}
\end{equation}
Over \qty{14}{\day}, the average payload data rate is then:
\begin{equation}
  R_\text{payload,avg} = \frac{\text{Canada Size}}{\qty{14}{\day}}=\qty{573.78}{\kilo\byte\per\second}
\end{equation}

This does not include the housekeeping data specified in the mission requirements and summarized in Table~\ref{tab:housekeepingdata} below.
\begin{table}[hb]
  \centering
  \captionsetup{width=.75\linewidth,font=small,labelfont=bf}
  \begin{tabular}{c|rl}
    \toprule
    Data & Quantity & Unit\\
    \midrule
    Error Detection & \num{3} & \si{\bit\per\byte}\\
    Latitude & \num{32} & \si{\bit\per image}\\
    Longitude & \num{32} & \si{\bit\per image}\\
    Altitude & \num{32} & \si{\bit\per image}\\
    Time & \num{64} & \si{\bit\per image}\\
    Synchronization & \num{24} & \si{\bit\per image}\\
    Health Data Rate & \num{26.66}\dots & \si{\bit\per\second}\\
    \bottomrule
  \end{tabular}
  \caption{Summary of required housekeeping data per mission requirements.}
  \label{tab:housekeepingdata}
\end{table}

\noindent The total housekeeping data per image can then be found via
\begin{multline}
  \text{Housekeeping per Image} = \text{Image Size}\times\text{Error Detection}+\text{Latitude}+\text{Longitude}\\+\text{Altitude}+\text{Time}+\text{Synchronization} = \qty{300}{\mega\byte\per image}
\end{multline}
The total housekeeping data per Canada:
\begin{equation}
  \text{Housekeeping Size} = \text{Housekeeping per Image} \times \text{Images per Canada} = \qty{260.27}{\giga\byte}
\end{equation}
And the average housekeeping data rate:
\begin{equation}
  R_\text{housekeeping,avg} = \frac{\text{Housekeeping Size}}{\qty{14}{\day}}+\text{Health Data Rate}=\qty{215.17}{\kilo\byte\per\second}
\end{equation}
To penultimately culminate in the \textit{average} downlink data rate:
\begin{equation}\label{eq:avgdownlinkdatarate}
  R_\text{DL,avg}=R_\text{payload,avg}+R_\text{housekeeping,avg}=\qty{788.95}{\kilo\byte\per\second}
\end{equation}
And as found in Appendix~\ref{app:annulus}, the proportion of time SARGE is within \ang{10} elevation of Gatineau is \qty{39.69}{\percent}, and thus the total access time is:
\begin{equation}\label{eq:totalaccess}
  T_\text{access} = P\times\qty{39.69}{\percent}\approx\qty{9.5}{\hour\per\day}
\end{equation}
From the guidance given in class, approximately \qty{20}{\percent} of access window should be allocated to uplink, thus the downlink window is \qty{80}{\percent} of $T_\text{access}$, and the actual downlink rate can be found:
\begin{equation}
  R_\text{DL} = \frac{R_\text{DL,avg}}{\frac{\qty{80}{\percent}\times T_\text{access}}{P}}=\qty{2.485}{\mega\byte\per\second}
\end{equation}
So the downlink rate required is about \qty{2.485}{\mega\byte\per\second}, which transmits for about \qty{7.6}{\hour} every sidereal day.
The bandwidth for QPSK (our downlink encoding scheme) is:
\begin{equation}
  B=0.6R=\qty{11.928}{\mega\hertz}
  \label{eq:downlinkbw}
\end{equation}

Then, as noted in Section~\ref{sec:configuration}, the communications satellite on SARGE is a parabolic antenna with a diameter $D_t$ of \qty{0.5}{\meter}.
Assuming a transmission efficiency $\eta_t$ of \qty{50}{\percent}, and noting that the wavelength $\lambda$ of the downlink center frequency of \qty{7.275}{\giga\hertz} is \qty{4.12}{\milli\meter}, the predicted gain is
\begin{equation}\label{eq:100}
  G_t=\eta_t\left(\frac{\pi D_t}{\lambda}\right)^2=\num{726}
\end{equation}

The path loss for the downlink direction is:
\begin{equation}\label{eq:101}
  L_\text{path}=\left(\frac{4\pi d}{\lambda}\right)^2\approx\num{6.53e-21}
\end{equation}
And the pointing accuracy loss can be estimated by finding the $\theta_{\qty{3}{\decibel}}$ angle via the relationship in slide deck 6:
\begin{equation}
  \theta_{\qty{3}{\decibel}}\approx\ang{70}\frac{\lambda}{D}=\ang{5.77}
\end{equation}
and then, assuming a pointing error $\epsilon$ of \ang{1} for the spacecraft:
\begin{equation}\label{eq:302}
  [L_\text{point}]=12\left(\frac{\epsilon}{\theta_{\qty{3}{\decibel}}}\right)^2=\qty{0.361}{\decibel}
\end{equation}

And finally, to find the required carrier to noise ratio, with a minimum bit error rate ${BER}$ of \num{10e-5} for the downlink, as suggested in slide deck 6:
\begin{equation}\label{eq:102}
  {C/N}_\text{required}=\frac RB\ln\left(\frac{1}{2{BER}}\right)=\qty{14.20}{\decibel}
\end{equation}

Whew.
\subsection{Up}
The uplink analysis is much the same as the downlink analysis presented just previously, except we just assume a transmission rate of \qty{2.5}{\kilo\bit\per\second}, and we're using BFSK as recommended in slide deck 6.
As well, for lack of better information and based on the ballparks present in the SME-SMAD, we assume a transmitter power at the basestation of \qty{200}{\watt}.
From Natural Resources Canada, the diameter of the Gatineau satellite dish is \qty{13}{\meter}, and we'll assume a pointing accuracy $\epsilon$ of \ang{0.25} and still a transmit efficiency $\eta_t$ of \qty{50}{\percent}.
Then the transmitter gain is:
\begin{equation}\label{eq:200}
  G_t=\eta_t\left(\frac{\pi D_t}{\lambda}\right)^2=\num{594e3}
\end{equation}
And the path loss is slightly different because the uplink center frequency is \qty{8.00}{\giga\hertz} with a corresponding wavelength $\lambda$ of \qty{3.75}{\milli\meter}:
\begin{equation}\label{eq:203}
  L_\text{path}=\left(\frac{4\pi d}{\lambda}\right)^2\approx\num{5.40e-21}
\end{equation}
And the $\theta_{\qty{3}{\decibel}}$:
\begin{equation}
  \theta_{\qty{3}{\decibel}}\approx\ang{70}\frac{\lambda}{D}=\ang{0.20}
\end{equation}
With a pointing loss of:
\begin{equation}\label{eq:303}
  [L_\text{point}]=12\left(\frac{\epsilon}{\theta_{\qty{3}{\decibel}}}\right)^2=\qty{18.42}{\decibel}
\end{equation}
A bandwidth of (according to slide deck 6):
\begin{align}
  B =2R(1+\beta)&=\qty{5016}{\hertz}\\\label{eq:201}
  \beta =\Delta f/f_{mod}&=\num{0.003125}\\
  \Delta f&=\qty{25}{\mega\hertz}\qquad(\text{Half of max channel BW})
\end{align}

And finally, the minimum carrier to noise is calculated in the same was as Eq.~\ref{eq:102}, but with a ${BER}$ of \num{10e-7} for telecommand, also as mentioned in slide deck 6:
\begin{equation}\label{eq:202}
  {C/N}_\text{required}=\frac RB\ln\left(\frac{1}{2{BER}}\right)=\qty{8.16}{\decibel}
\end{equation}
\clearpage
\section{Referenced Tables and Figures}\label{app:refs}
\begin{figure}[h]
  \centering
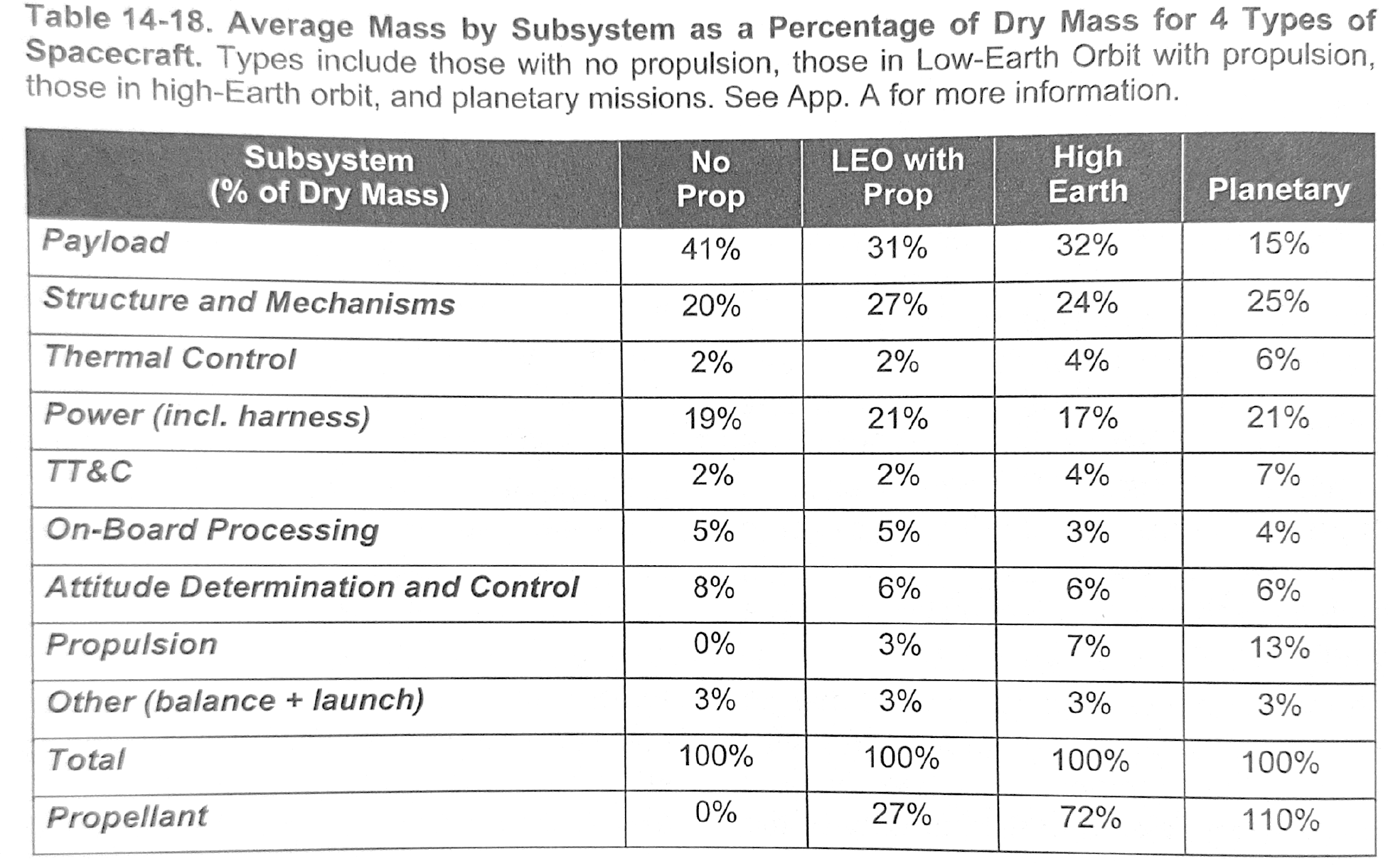
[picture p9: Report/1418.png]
  
  \caption{Table 14-18 in SME-SMAD~\cite[p. 422]{sme}.}
  \label{fig:1418}
\end{figure}
\begin{figure}[h]
  \centering
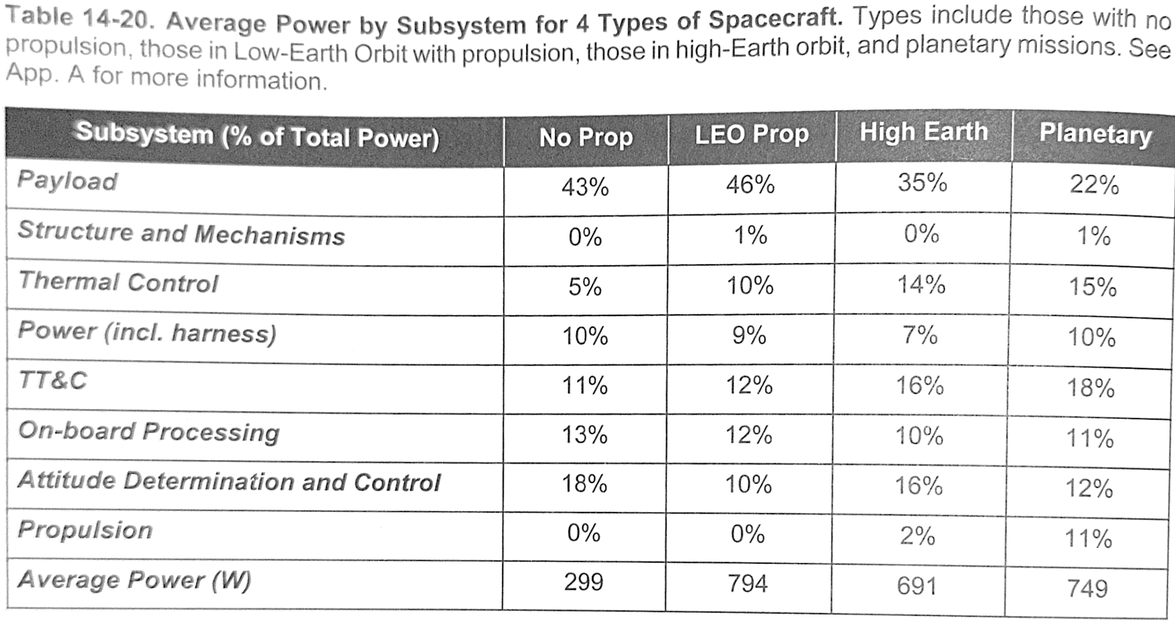
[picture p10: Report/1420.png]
  
  \caption{Table 14-20 in SME-SMAD~\cite[p. 424]{sme}.}
  \label{fig:1420}
\end{figure}
\begin{figure}[h]
  \centering
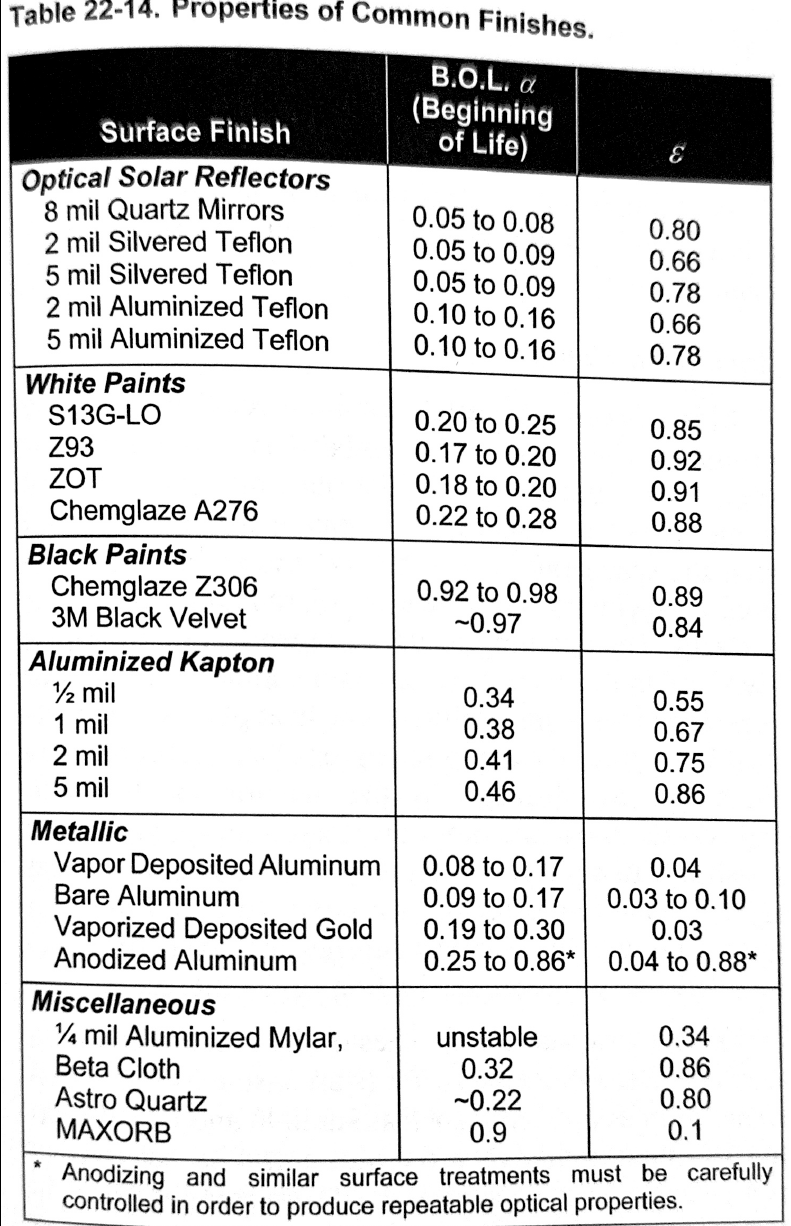
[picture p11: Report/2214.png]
  
  \caption{Table 22-14 in SME-SMAD~\cite[p. 695]{sme}.}
  \label{fig:2214}
\end{figure}
\begin{figure}[h]
  \centering
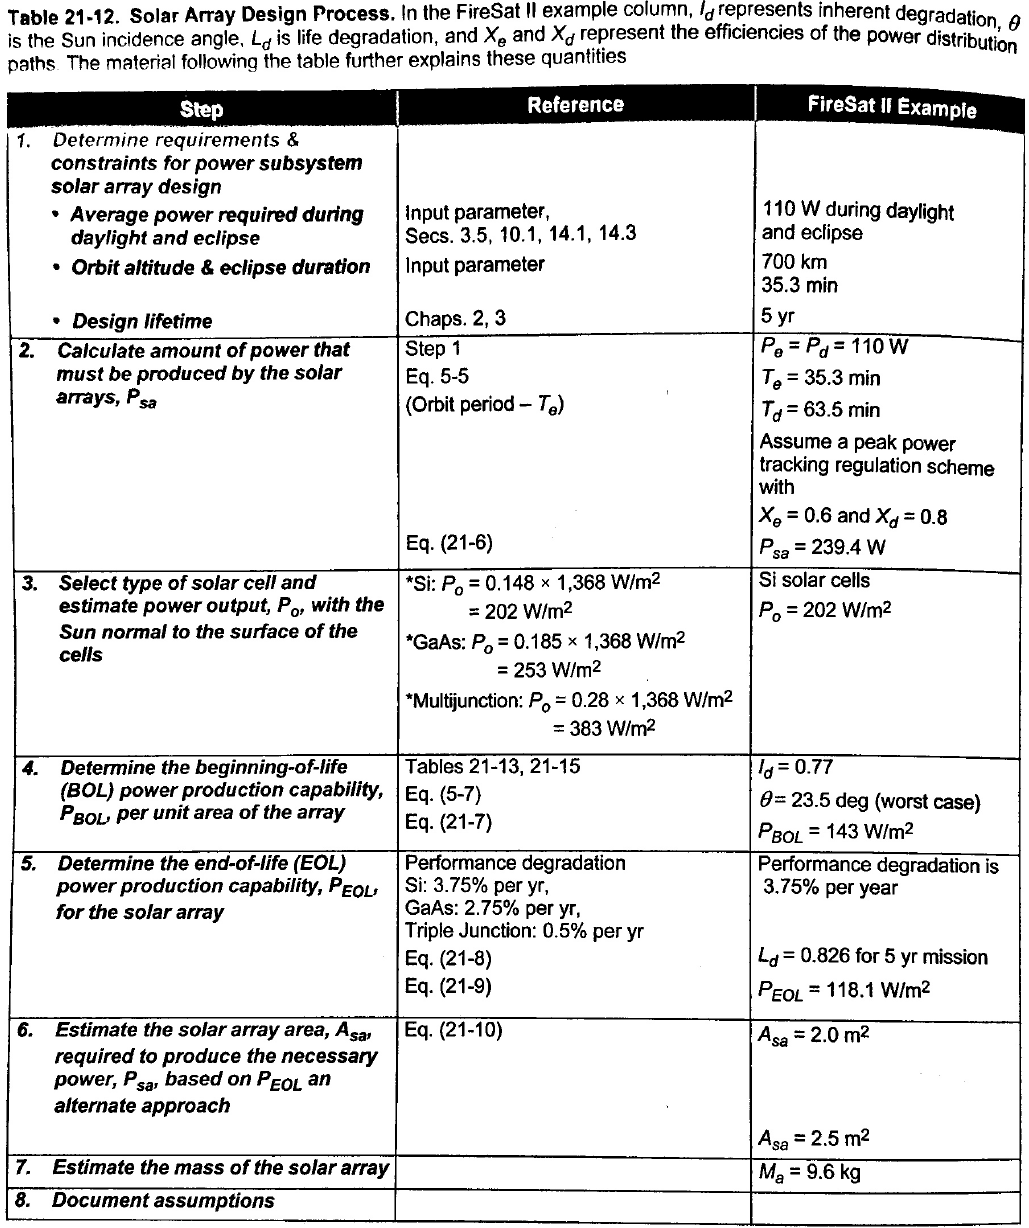
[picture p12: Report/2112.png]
  
  \caption{Table 21-12 in SME-SMAD~\cite[p. 644]{sme}.}
  \label{fig:2112}
\end{figure}

\clearpage
\section{Orbital Transfer Calculations}\label{app:orbcalcs}
figure

\vfill
\section{Preliminary Drawings}\label{app:julia}

\end{document}

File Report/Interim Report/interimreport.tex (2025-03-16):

\documentclass[9pt]{article}
\usepackage[letterpaper, margin=2cm]{geometry}
\usepackage[utf8]{inputenc}
\usepackage[sfdefault]{inter}
\usepackage[T1]{fontenc}
\usepackage{amsmath}
\usepackage{graphicx, caption}
\usepackage{xcolor}
\usepackage{subcaption}
\usepackage{siunitx}
\usepackage{booktabs}
\usepackage{tabularx}
\let\temp\rmdefault
\usepackage{fourier}
\let\rmdefault\temp

\usepackage[
  backend=biber,
  style=ieee
]{biblatex}
\addbibresource{spacecraft.bib}

% Title Page
\title{\Huge SARGE\\\Large Preliminary Report}
\author{Jimmy Vaughan\\(101 156 687)}

\begin{document}
\begin{figure}[t]
  \centering
  
\end{figure}
\maketitle
\tableofcontents
\pagenumbering{gobble}
\clearpage
\pagenumbering{arabic}
\section{Introduction}
This preliminary report is intended to inform the reader of the progress made on developing the SARGE satellite.
SARGE stands for \textbf{S}ynthetic~\textbf{A}perture~\textbf{R}adar:~\textbf{G}reenhouse~\textbf{E}missions, a satellite platform designed to monitor for potential leaks of cross-Canada pipelines using synthetic aperture radar.

Good progress has been made towards developing the mass, power, and link budgets of the various subsystems.
Estimations have been made where necessary, and noted, and the development process permits back-filling these determinations with higher quality estimates as they become available.
Preliminary design drawings are available as the last appendix, Appendix~\ref{app:julia}.

\section{Orbit Selection}
The mission requirements state that the primary goal of this mission is to image the entirety of Canada at least every 14~days.
To satisfy this requirement, a geosynchronous orbit with a nonstandard inclination was chosen.
As shown in Figure~\ref{fig:groundtrack}, the ground track of a conical SAR with a minimum elevation angle of \ang{75} covers the entirety of contiguous Canada.

\begin{figure}[hb]
  \centering
  \captionsetup{width=.75\linewidth,font={small},labelfont={bf}}
  
  \caption{Ground swath of SARGE over continental Canada. Ground stations are shown in teal and sky blue, and the majority of Canada is outlined in red ($A\approx\qty{8.342e6}{\square\kilo\metre}$). The magenta circles show the coverage of the SAR beam at some discrete points in time.}
  \label{fig:groundtrack}
\end{figure}

The orbital parameters are summarized in Table~\ref{tab:orbit}.
We can see that the chosen orbit is a circular retrograde orbit with a period of about one sidereal day.
This regularity allows the satellite to image, process, and transmit one~fourteenth of Canada each day, with a consistent and regular ground station access window.

\begin{table}[h]
  \centering
  \captionsetup{width=.75\linewidth,font={small},labelfont={bf}}
    \begin{tabular}{r S|r S}
      \toprule
      \multicolumn{4}{c}{Basic Orbital Parameters}\\
      \midrule
      Period $P$ & \qty{86170.5}{\second} & Arg. of Perigee $\omega$ & \ang{0} \\
      Eccentricity $\epsilon$ & \num{0.0} & LAN $\Omega$ & \ang{50} \\
      Inclinination $i$ & \ang{121} & True Anomaly $\nu$ & \ang{30} \\
      \midrule %\midrule
      \multicolumn{4}{c}{Derived Quantities}\\
      \midrule
      Orbit Radius $r$ & \qty{42166.26}{\kilo\metre} & Orbital Altitude $h$ & \qty{35788.12}{\kilo\metre} \\
      Velocity $v$ & \qty{3.074}{\kilo\metre\per\second} & Orbits per Day $n$ & \qty{1.002663}{\per\day} \\
      \bottomrule
    \end{tabular}
    \caption{Orbital parameters and convenient derived quantities.}
    \label{tab:orbit}
\end{table}

At high altitudes, like GEO, the gravitational forces of the Sun and the Moon become significant, but air drag is generally negligible~\cite{sse}.
The stationkeeping consequences are explored in Appendix~\ref{app:stnkeep}.

\section{Mass Budget}
According to David Everett of the NASA Goddard Space Flight Center, author of Chapter 14 ``Overview of Spacecraft Design'' in SME-SMAD, the first of the three steps of mass estimation is ``A rough order of magnitude based on payload mass''~\cite[p. 399]{sme}.
Given that sentiment, and the preliminary nature of this report, I feel it is appropriate to base the initial mass estimate on what is described to be data representative of mission type \textit{and} historical data given in Table~14-18~\cite[p. 422]{sme}, as summarized in Table~\ref{tab:mass}, with comments noted in the third column.

\begin{table}[h]
  \centering
  \captionsetup{width=.75\linewidth,font={small},labelfont={bf}}
  %\begin{tabularx}{.8\linewidth}{l|r r X}
  \begin{tabular}{l|r r l}
    \toprule
    Subsystem & Mass\% & Mass & Comments \\
    \midrule
    Payload & \qty{32}{\percent} & \qty{200}{\kilo\gram} & Provided in requirements \\
    Structure \& Mechanisms & \qty{24}{\percent} & \qty{150}{\kilo\gram} & Table~14-18 \\
    Thermal Control & \qty{4}{\percent} & \qty{25.}{\kilo\gram} & ''\\
    Power (incl. harness) & \qty{17}{\percent} & \qty{106}{\kilo\gram}&''\\
    TT\&C & \qty{4}{\percent} & \qty{25}{\kilo\gram}&''\\
    Data Processing & \qty{3}{\percent} & \qty{19}{\kilo\gram}&''\\
    ADCS & \qty{6}{\percent} & \qty{37}{\kilo\gram}&''\\
    Propulsion & \qty{7}{\percent} & \qty{44}{\kilo\gram}&''\\
    Other & \qty{3}{\percent} & \qty{19}{\kilo\gram}&''\\
    \midrule 
    Total Dry Mass & \qty{100}{\percent} & \qty{625}{\kilo\gram} & \\
    Propellant & \qty{72}{\percent} & \qty{450}{\kilo\gram} & May need less (see Appendix~\ref{app:stnkeep})\\
    \midrule 
    Wet Mass & & \qty{1075}{\kilo\gram} & \\
    \bottomrule
  \end{tabular}
  \caption{Preliminary mass budget estimation, based on provided payload mass and the listing for ``High Earth'' in the SME-SMAD~\cite{sme}.}
  \label{tab:mass}
\end{table}

\section{Power Budget}
Like the Mass Budget in Table~\ref{tab:mass}, the preliminary power budget below in Table~\ref{tab:power} is based on David~Everett's chapter of the SME-SMAD.
  This time, however, a modification to the suggested weights in Table~14-20~\cite[p. 424]{sme}, since no power was allocated to the Structure~\&~Mechanisms subsystem.
As noted in Section~\ref{sec:configuration}, there are several non-oneshot mechanisms on SARGE that will require power.
  The payload mass proportion was thus lessened by \qty{2}{\percent}, from \qty{35}{\percent} to \qty{33}{\percent} to give a corresponding mass proportion of \qty{2}{\percent} to the Structures~\&~Mechanisms subsystem.

\begin{table}[h]
  \centering
  \captionsetup{width=.75\linewidth,font={small},labelfont={bf}}
  \begin{tabular}{l|r r l}
    \toprule
    Subsystem & Power\% & Avg. Power & Comments \\
    \midrule
    Payload & \qty{33}{\percent} & \qty{350}{\watt} & Specified in requirements, mod. from Table~14-20 \\ 
    Structure \& Mechanisms & \qty{2}{\percent} & \qty{21}{\watt} & Mod. from Table~14-20 \\
    Thermal & \qty{14}{\percent} & \qty{148}{\watt} & Table~14-20 \\
    Power (incl. harness) & \qty{7}{\percent} & \qty{74}{\watt} & ''\\
    TT\&C & \qty{16}{\percent} & \qty{170}{\watt} & ''\\
    Data Processing & \qty{10}{\percent} & \qty{106}{\watt} &''\\
    ADCS & \qty{16}{\percent} & \qty{170}{\watt}&''\\
    Propulstion & \qty{2}{\percent} & \qty{21}{\watt} & ''\\
    \midrule
    Total & \qty{100}{\percent} & \qty{1061}{\watt} &\\
    \bottomrule
  \end{tabular}
  \caption{Preliminary power budget estimation, based on provided payload mass and the listing for ``High Earth'' in the SME-SMAD~\cite{sme}, modified to allow for powered mechanisms.}
  \label{tab:power}
\end{table}

\section{Link Budget}
Based on both slide deck 6, ``TTC'', and select portions of the SME-SMAD, the uplink and downlink link budgets are summarized in Table~\ref{tab:link}.
As well, the downlink and uplink frequencies were chosen according to Professor~Jim~Wight's course handout for ELEC~4509.
It's noted in that handout that frequency ranges 7.25-7.30~GHz and 7.975-8.025~GHz are reserved for downlink and uplink satellite communications, respectively~\cite[II, p. 3]{commlinks}.
\begin{table}[h]
  \centering
  \captionsetup{width=.75\linewidth,font=small,labelfont=bf}
  \begin{tabular}{c|rl|l}
    \toprule
    Uplink & Value & Unit & Comments \\
    \midrule
    $P_t$ & \num{23.01} & \si{\decibel\watt} & \qty{200}{\watt} ground transmitter assumed\\
    $G_t$ & \num{57.74} & \si{\decibel} & Eq.~\ref{eq:200}\\
    $L_\text{path}$ & \num{202.68} & \si{\decibel} & Eq.~\ref{eq:203}\\
    $L_\text{point}$ & \num{18.42} & \si{\decibel} & Eq.~\ref{eq:303}\\
    $L_\text{atmosphere}$ & \num{10.00} & \si{\decibel} & Assumed\\
    $k$ & \num{-228.60} & \si{\decibel\joule\per\kelvin} & \\
    $B$ & \num{37.00} & \si{\decibel\hertz} & Eq.~\ref{eq:201}\\
    $G_r$ & \num{28.61} & \si{\decibel} & Eq.~\ref{eq:100}\\
    $T$ & \num{27.00} & \si{\decibel\kelvin} & Assumed\\
    \midrule
    ${C/N}_\text{achieved}$ & \num{55.54} & \si{\decibel} & Eq.~\ref{eq:uplinkachieved}\\
    ${C/N}_\text{required}$ & \num{8.16} & \si{\decibel} & Eq.~\ref{eq:202}\\
    \midrule
    Margin & \num{47.39} & \si{\decibel}& \\
    \bottomrule \toprule
    Downlink & Value & Unit & Comments\\
    $P_t$ & \num{20.00} & \si{\decibel\watt} & \qty{100}{\watt} of \qty{170}{\watt} estimated in power budget\\
    $G_t$ & \num{28.61} & \si{\decibel} & Eq.~\ref{eq:100}\\
    $L_\text{path}$ & \num{201.85} & \si{\decibel} & Eq.~\ref{eq:101}\\
    $L_\text{point}$ & \num{0.36} & \si{\decibel} & Eq.~\ref{eq:302}\\
    $L_\text{atmosphere}$ & \num{10.00} & \si{\decibel} & Assumed\\
    $k$ & \num{-228.60} & \si{\decibel\joule\per\kelvin} & \\
    $B$ & \num{70.77} & \si{\decibel\hertz} & Eq.~\ref{eq:downlinkbw}\\
    $G/T$ & \num{46.94} & \si{\decibel\per\kelvin} & Eq.~\ref{eq:minGT}\\
    \midrule
    ${C/N}_\text{achieved}$ & \num{41.17} & \si{\decibel} & Eq.~\ref{eq:downlinkachieved}\\
    ${C/N}_\text{required}$ & \num{11.52} & \si{\decibel} & Eq.~\ref{eq:102}\\
    \midrule
    Margin & \num{29.65} & \si{\decibel} & \\
    \bottomrule
  \end{tabular}
  \caption{Preliminary link budget, based on noted assumptions and analyses detailed in Appendix~\ref{app:linkbudget}.}
  \label{tab:link}
\end{table}

The uplink ${C/N}_\text{achieved}$ was calculated using the following expression, where square brackets indicate logarithmic quantities:
\begin{equation}\label{eq:uplinkachieved}
  [C/N]_\text{achieved}=[P_t] + [G_t] + [G_r] - [L_\text{path}] - [L_\text{point}] - [L_\text{atmosphere}] - [k] -[T]-[B]
\end{equation}
Whereas the downlink ${C/N}_\text{achieved}$ was calculated using a slightly different methodology, where the minimum certifiable $G/T$ figure is found by~\cite[I, p. 40]{commlinks}:
\begin{equation}\label{eq:minGT}
  \frac GT\ge \qty{40.7}{\decibel}+20\log{\frac f4}
\end{equation}
where $G/T$ is in \si{\decibel\per\kelvin}, and $f$ is in \si{\giga\hertz}.
Since that's the minimum figure of merit to be certified for a ground station, I took that as the figure of merit for Gatineau.
Then,
\begin{equation}\label{eq:downlinkachieved}
  {C/N}_\text{achieved}=[P_t]+[G_t]+\left[\frac GT\right]-[L_\text{path}]-[L_\text{point}]-[L_\text{atmosphere}]-[k]-[B]
\end{equation}

\section{Configuration}\label{sec:configuration}
The configuration of SARGE is a nadir-pointing 3-axis stabilized solar-powered satellite.
An annotated isometric view of the preliminary design/layout is shown in Figure~\ref{fig:iso}.

\begin{figure}[h]
  \centering
  \captionsetup{width=.75\linewidth,font=small,labelfont=bf}
  
  \caption{Isometric view of the satellite with annotation in red to aid understanding.}
  \label{fig:iso}
\end{figure}

As can hopefully be seen, the major components currently include 2 solar arrays, articulated only for launching, via single-shot hinges at each meeting point.
These arrays are gimbaled in one axis, shown in the front view, Figure~\ref{fig:front}.
The direction of travel is shown in Figure~\ref{fig:iso}, as well as the nadir pointing direction.

\begin{figure}[h]
  \centering
  \captionsetup{width=.75\linewidth,font=small,labelfont=bf}
  
  \caption{Front view of SARGE with annotation in red. One of the solar panel arrays is hidden so as not to obstruct the interior of the frame.}
  \label{fig:front}
\end{figure}

Since the masses of the solar arrays are identical, and they are symmetric about the nadir axis, and since the mass proportion of the payload is only around \qty{32}{\percent} of the total dry mass, the remaining subsystems should make it so that the center of mass is not located within the payload container.
This means that an ADCS system with reaction wheels should be able to be located directly in line with all three axes relative to the center of inertia, so pointing should be easily controllable.
The remaining subsystems will all ideally fit in the remaining payload-sized area to the right of the payload in Figure~\ref{fig:front}.

More engineering drawings are available in Appendix~\ref{app:julia}.

\section{Conclusions}
Although further analysis is required to ensure that the current configuration can reject/retain enough heat, and the delta V budget is yet to be done, the current iteration of SARGE looks to be reasonable.
The mass distribution and total mass falls within the ranges typical of a GEO mission.
The total estimated power draw is somewhat lower than what is mentioned in the course slides.
The link budget has good margins, even after adding an assumed atmospheric loss.

\clearpage
\appendix

\printbibliography
\clearpage
\section{Orbital Perturbations and $\Delta V$}\label{app:orbpert}

SME-SMAD equations (9-46) and (9-47) on pg.~219 give approximate worse case $\Delta V$ relations per year~\cite{sme}:
\begin{align}
  {\Delta V}_\text{Moon} &= 102.67\cos\alpha\sin\alpha\hspace{2em}\text{(m/s per year)}\\
  {\Delta V}_\text{Sun} &= 40.17\cos\gamma\sin\gamma\hspace{2.7em}\text{(m/s per year)}
\end{align}
where $\alpha$ is the angle between the orbit plane and the Moon's orbit, and $\gamma$ is the angle between the orbit plane and the ecliptic.

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

The transverse (East-West) stationkeeping requirement is mentioned as about \qty{10}{\percent} of the North-South stationkeeping requirements~\cite{sme}, however I believe that the high inclination of SARGE will work against us in this scenario, as the oblateness of Earth around the equator will have a more pronounced effect for orbits that do not closely follow the equator.
As well, this oblateness likely has an effect on the North-South stationkeeping, since we're dealing with neither a polar nor equatorial orbit.
For this reason, I'm going to estimate the East-West stationkeeping to be equal to the North-South:
\begin{equation}
  {\Delta V}_{EW} = {\Delta V}_{NS} = \qty{47.85}{\meter\per\second}%pg 219
\end{equation}
This ought to roughly account for the stationkeeping requirements of the spacecraft at this stage of design. 

\subsection{Orbital Transfer}
Placing a satellite in GEO usually entails delivery from a launch plaftorm to a GTO, then some sort of transfer into GEO.
I will budget for and deal with this later, when I consider the launch platform.

\subsection{Decommissioning}

The SME-SMAD recommends handling the special scarcity and properties of the GEO orbit (specifically its vulnerability to debris and junk) by raising spacecraft \qty{500}{\kilo\metre} above GEO at the end of their life.
The $\Delta V$ required for that is
\begin{equation}
  {\Delta V}_\text{disposal} = \qty{18}{\metre\per\second}
\end{equation}
from SME-SMAD page 233 for decommissioning a GEO satellite~\cite{sme}, and the propellant mass will be found at a later date after an in-depth $\Delta V$ analysis.

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

\begin{figure}[h]
  \centering
  \captionsetup{width=.75\linewidth,font=small,labelfont=bf}
  
  \caption{Demonstration of zero eclipse time via STK 3D view. The sun is visible just over the horizon.}
  \label{fig:eclipse}
\end{figure}

\subsection{Configuration Choices}
In order to accomodate the necessary surface area of the solar panels in a compact way with margins to account for structural frames that would block cells of the solar array, and to pre-emptively take into account the packing of the spacecraft into a launch platform, a quick sketch (Figure~\ref{fig:solarsketch}) showed that the structure should follow roughly a form factor of $\SI{1}{\meter}\times\SI{1}{\meter}\times\SI{0.5}{\meter}$.
This allows the compact packing of nominally \SI{6}{\square\meter} of solar panels, which well exceeds the required \SI{4.26}{\square\meter}.
In later analysis, it will be shown how much of a margin we have to block that area with support structures when EOL conditions and degradation is taken into account.

Table~21-5 in the SME-SMAD notes that travelling wave tube amplifiers (TWTA)s are about 50-60\% efficient for X-band and weigh about \qty{2.5}{\kilo\gram} including power converter~\cite[p. 637]{sme}.
Table~16-16 in the SME-SMAD notes that parabolic reflectors weigh between 10-30~kg~\cite[p. 484]{sme}.

\clearpage
\section{Fun!}
This section is named ``Fun!'' unironically -- these were fun.

\subsection{Fun Annulus Geometry}\label{app:annulus}
To approximate the arc angle subtended by the \ang{10} elevation $\delta$ access requirement, I created a quick sketch shown in Figure~\ref{fig:annulus} to wrap my head around the geometry.
I then used the formula for worst-case distance $d$ from slide deck 6 to find the corresponding half angle $\gamma$:
\begin{equation}
  d=R_\text{Earth}\left(
    \sqrt{\left(\frac{r}{R_\text{Earth}}\right)^2-\cos^2\delta}
    -\sin\delta
  \right)
\end{equation}
From my sketch,
\begin{equation}
  \gamma = \sin^{-1}\left(\frac{d\sin(\ang{90}+\delta)}{r}\right)
\end{equation}
And thus the access ratio is the ratio between the access arc and the total arc (circumference):
\begin{equation}
  \text{Access Ratio} = \frac{2\gamma r}{2\pi r} = \qty{39.69}{\percent}
\end{equation}

\begin{figure}[h]
  \centering
  \captionsetup{width=.75\linewidth,font=small,labelfont=bf}
  
  \caption{Figuring out the geometry to find the half-angle from the center of the Earth given the radius and elevation [Own work].}
  \label{fig:annulus}
\end{figure}

This makes a lot of sense -- SARGE is far away, the elevation angle of \ang{10} is pretty generous, and the groundtrack passes fairly close to Gatineau station (on a global scale, at least).

\subsection{Fun Orbital Plane Geometry}\label{app:orbplanes}

To find $\alpha$ and $\gamma$ for the orbital perturbation estimations in Appendix~\ref{app:orbpert}, I estimated the angles between SARGE's orbital plane and the Sun and the Moon using the Ecliptic plane and Lunar orbit inclination values found in a figure (with no listed author) from Wikipedia.

\begin{figure}[hb]
  \centering
  \captionsetup{width=.75\linewidth,font={small},labelfont={bf}}
  
  \caption{Angles between the orbit plane of SARGE and the Lunar orbit plane ($\alpha$) and the Ecliptic plane ($\gamma$). [Author unknown, \texttt{CC0}, annotations (in colour) added]}
  \label{fig:moonorbit}
\end{figure}

From Figure~\ref{fig:moonorbit}, we can estimate that the angle between SARGE's orbit plane and the Ecliptic plane ($\gamma$) to be \ang{97.56}, and between SARGE's orbit plane and the Lunar orbit plane ($\alpha$) as \ang{92.42}.

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

This does not include the housekeeping data specified in the mission requirements and summarized in Table~\ref{tab:housekeepingdata} below.
\begin{table}[hb]
  \centering
  \captionsetup{width=.75\linewidth,font=small,labelfont=bf}
  \begin{tabular}{c|rl}
    \toprule
    Data & Quantity & Unit\\
    \midrule
    Error Detection & \num{3} & \si{\bit\per\byte}\\
    Latitude & \num{32} & \si{\bit\per image}\\
    Longitude & \num{32} & \si{\bit\per image}\\
    Altitude & \num{32} & \si{\bit\per image}\\
    Time & \num{64} & \si{\bit\per image}\\
    Synchronization & \num{24} & \si{\bit\per image}\\
    Health Data Rate & \num{26.66}\dots & \si{\bit\per\second}\\
    \bottomrule
  \end{tabular}
  \caption{Summary of required housekeeping data per mission requirements.}
  \label{tab:housekeepingdata}
\end{table}

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

Then, as noted in Section~\ref{sec:configuration}, the communications satellite on SARGE is a parabolic antenna with a diameter $D_t$ of \qty{0.5}{\meter}.
Assuming a transmission efficiency $\eta_t$ of \qty{50}{\percent}, and noting that the wavelength $\lambda$ of the downlink center frequency of \qty{7.275}{\giga\hertz} is \qty{4.12}{\milli\meter}, the predicted gain is
\begin{equation}\label{eq:100}
  G_t=\eta_t\left(\frac{\pi D_t}{\lambda}\right)^2=\num{726}
\end{equation}

The path loss for the downlink direction is:
\begin{equation}\label{eq:101}
  L_\text{path}=\left(\frac{4\pi d}{\lambda}\right)^2\approx\num{6.53e-21}
\end{equation}
And the pointing accuracy loss can be estimated by finding the $\theta_{\qty{3}{\decibel}}$ angle via the relationship in slide deck 6:
\begin{equation}
  \theta_{\qty{3}{\decibel}}\approx\ang{70}\frac{\lambda}{D}=\ang{5.77}
\end{equation}
and then, assuming a pointing error $\epsilon$ of \ang{1} for the spacecraft:
\begin{equation}\label{eq:302}
  [L_\text{point}]=12\left(\frac{\epsilon}{\theta_{\qty{3}{\decibel}}}\right)^2=\qty{0.361}{\decibel}
\end{equation}

And finally, to find the required carrier to noise ratio, with a minimum bit error rate ${BER}$ of \num{10e-5} for the downlink, as suggested in slide deck 6:
\begin{equation}\label{eq:102}
  {C/N}_\text{required}=\frac RB\ln\left(\frac{1}{2{BER}}\right)=\qty{14.20}{\decibel}
\end{equation}

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

And finally, the minimum carrier to noise is calculated in the same was as Eq.~\ref{eq:102}, but with a ${BER}$ of \num{10e-7} for telecommand, also as mentioned in slide deck 6:
\begin{equation}\label{eq:202}
  {C/N}_\text{required}=\frac RB\ln\left(\frac{1}{2{BER}}\right)=\qty{8.16}{\decibel}
\end{equation}

\vfill
\section{Preliminary Drawings}\label{app:julia}

\end{document}

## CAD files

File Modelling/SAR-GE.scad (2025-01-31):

// SAR-GE Solid Model
// Copyright (C) 2025  James Vaughan
// This program is free software: you can redistribute it and/or modify
// it under the terms of the GNU General Public License as published by
// the Free Software Foundation, either version 3 of the License, or
// (at your option) any later version.
//
// This program is distributed in the hope that it will be useful,
// but WITHOUT ANY WARRANTY; without even the implied warranty of
// MERCHANTABILITY or FITNESS FOR A PARTICULAR PURPOSE.  See the
// GNU General Public License for more details.
// 
// You should have received a copy of the GNU General Public License
// along with this program.  If not, see <https://www.gnu.org/licenses/>.

// Payload
square(0.5, true);
linear_extrude(height=1, center=false, convexity=0, twist=0, slices=1, scale=1.0);

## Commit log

2025-01-31 FOSS or bust, even modelling
    [SAR-GE.scad]
2025-03-16 Interim report and analysis
    Committed after submission date, to avoid chance of plagiarism.
    Will commit more regularly from now on, but may not push until after
    final report submission.
    [SARGE.ods]
2025-04-02 Finish Delta V budget
    [SARGE.ods]
2025-04-06 Finalize mass, power, and comms budgets
2025-04-07 Finish power and thermal subsystems
